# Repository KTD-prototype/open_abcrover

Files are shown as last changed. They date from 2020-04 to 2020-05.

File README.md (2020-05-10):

<!-- # open_abcrover -->

<div align="center">

</div>

<br>
<br>

- [Overview](#overview)
  - [General information](#general-information)
  - [How does it moves](#how-does-it-moves)
  - [Basic spesification](#basic-spesification)
- [Operability confirmed environments](#operability-confirmed-environments)
  - [PC environments (both develop and operate)](#pc-environments-both-develop-and-operate)
  - [Peripherals](#peripherals)
  - [Packages](#packages)
- [Parts list, assembly and wiring](#parts-list-assembly-and-wiring)
- [Install Software](#install-software)
  - [Install, download and build related packages](#install-download-and-build-related-packages)
  - [Prepare sub-onboard comtroller : arduino mega or equivalents](#prepare-sub-onboard-comtroller--arduino-mega-or-equivalents)
- [How to use](#how-to-use)
  - [Power source](#power-source)
  - [Check before operation](#check-before-operation)
  - [Launch!](#launch)
  - [Discription](#discription)

# Overview
## General information
This is an open source, affordable ground platform for remote-operated & autonomous driving experiments.
It is :  
* Simple and Expandable
    * Universal aluminum extruded beams, easy to mount your hardware. 
    * 3D printed brackets and mounts easy to be customized
    * Customizable software components built on ROS<sup>TM</sup> <sup>[1](#note1)</sup> and Arduino, easy to add your own software and electronics. 
  
* All terrain driving
    * High power motor and big wheel
    * Moderate size for indoor use, same foot print as domestic robotic vacuums
    * Convertible brackets to boost up wheel base and tread width for stable outdoor locomotion

* Affordable
  * Cheap and easy-to-by components
  * Minimum hardwares and electronics for remote operation can be built with around $400 USD or ¥40,000 JPY

<small id="note1">ROS is a trademark of Open Robotics.</small>

<br>

## How does it moves
Link to my youtube.  

(https://www.youtube.com/watch?v=tylhsJ_iiBY)

<br>

## Basic spesification
|General||
|:--|:--|
|Dimensions|W 250 * D 250 * H 250 [mm] at minimum assembly|
|Foot prints|350 [mm] diameter circle|
|Battery capacity|120 Wh for up to 2 hours operation|
|Ground clearance|55 [mm]|
|Total weight|4 [kg]|

|Chassis||
|:--|:--|
|Frames|20 * 20 [mm] aluminum beams|
|Brackets|3D printed with PETG or carbon PETG|
|Additionals|You can mount more beams and add your hardwares by M4 bolts and nuts.|

|Drive trains||
|:--|:--|
|Motors|Geared, brushed DC motor with 37mm diameter, 317rpm @maximum spped, 3.6N・m @stall by [servocity](https://www.servocity.com/317-rpm-spur-gear-motor-w-encoder)|
|Wheels|6 inch diameter, driven wheels|
|Casters|3 inch diameter, passive casters|

|Electronics||
|:--|:--|
|PC|[Jetson Nano Developer Kit (ver.B01)](https://developer.nvidia.com/embedded/jetson-nano-developer-kit)|
|MPU|[Arduino Mega 2560 REV3](https://store.arduino.cc/usa/mega-2560-r3)|
|IMU sensor|9 axis sensor [Adafruit BNO055](https://learn.adafruit.com/adafruit-bno055-absolute-orientation-sensor)|
|Motor encoders|mounted on each motor axes|
|Cameras|(*not used by default*)  Sainsmart IMX219 night vision camera module with 160° FOV, 8MP relosution, active IR flash (discontinued? [equivalents](https://www.sainsmart.com/products/sainsmart-imx219-night-vision-camera-module-for-nvidia-jetson-nano-board-8mp-sensor-77-degree-fov)) |

<br>
<br>

# Operability confirmed environments
The open ABC rover is developed and tested conditions below. Of course, you can make any changes and modifications along with your preferences.
## PC environments (both develop and operate)
* Ubuntu 18.04 LTS
  * python2.7.17
  * ROS melodic

## Peripherals
* Main on-board computer : [Jetson Nano Developer Kit(ver.B01)](https://developer.nvidia.com/embedded/jetson-nano-developer-kit)
* Sub on-board controller : [Arduino Mega 2560 REV3](https://store.arduino.cc/usa/mega-2560-r3)
* Joy stick : [Logitec F710 wireless gamepad](https://www.logitechg.com/en-us/products/gamepads/f710-wireless-gamepad.940-000117.html)

## Packages
* wheel odometry for differential-drive wheeled robot : [wheel_odometry](https://github.com/KTD-prototype/wheel_odometry)
* joy signal processing : [joy - ROS Wiki](http://wiki.ros.org/joy)
* velocity command generator from joy : [joy_teleop - ROS Wiki](http://wiki.ros.org/joy_teleop)

<br>
<br>

# Parts list, assembly and wiring
***Detailed documents are arriving soon!***

<br>

One noticeable feature of this rover is it's convertibility between outdoor mode and indoor mode.  

As you can see in a schematic iamge below, you can flip or offset the brackets so that you can boost up or shrink the rover's wheel base and tread width.  

At left side of the image, it's outdoor mode with bigger wheel base and tread width, to improve stability on rough terrain. At right side, it's indoor mode with less foot print to improve smooth movement in narrow area.  

<br>

left : outdoor mode, right : indoor mode
<div align="center">left : outdoor mode, right : indoor mode</div>

<br>
<br>

# Install Software
## Install, download and build related packages
Assume your workspace are named as ~/catkin_ws
```
$ cd ~/catkin_ws/src
$ git clone git@github.com:KTD-prototype/open_abcrover.git #main package
$ git clone git@github.com:KTD-prototype/wheel_odometry.git #wheel odometry package
$ sudo apt install ros-melodic-joy ros-melodic-joystick-teleop #additional packages
$ cd ~/catkin_ws
$ catkin_make
```

## Prepare sub-onboard comtroller : arduino mega or equivalents
Pick up codes from the directroy you've downloaded ; .../open_abcrover/scripts/arduino/open_abcrover_control_v1.0  

Upload them to your own board. The main file is named : open_abcrover_control_v1.0.ino

<br>
<br>

# How to use
## Power source
Any types of batteies can be used. In testing, I used two 4-cell Li-po batteries(14.8V at nominal voltage) One for motors, another for on-board computer with DCDC convirsion into 5V via BEC (battery eliminator circuitry)

In my choice, maximum voltage acceptable to motors are 12V. In those case, you have to regulate motor command by your own script.

Be careful to use Li-po or Li-ion batteries, not to over-charge, over-discharge, damage batteries!

<br>

## Check before operation
* Power source connection?
* All peripherals connected? (e.g. USB wireless receiver for your joystick)
* No shorted circuit? Be super-carefule especially around power source wiring such as terminal blocks.
* Wheels and boards are firmly mounted?

<br>

## Launch!
Type as bellow at your terminal.
```
$ roslaunch open_abcrover teleop_sample.launch
```

This file launchs all relative nodes to test default settings for remote operation via your joystick.

<br>

## Discription
**Remote operation**  
Once you launched as discripted above, you can drive the rover by your joy stick.
By default, you can enable remote operation by button LB, and get the rover move by left joystick. The maximum speed for this mode is around **1 km/h**.

Furthermore, you can enable **TURBO** mode to raise the maximum speed up to **4 km/h** , by pressing A button.

Button assignment and labels are according to joystick I used : [Locitech F710](https://www.logitechg.com/en-us/products/gamepads/f710-wireless-gamepad.940-000117.html) with **X-Input** mode.

<br>

**Nodes**
* **/joy_node** : Receive signals from joystick and send as commands from an operator
* **/teleop_twist_joy** : Receive commands from an operator and convert into velocity commands. Also regulates maximum gains of the velocity control by those paramters.
* **/velocity_controller** : Receive the velocity commands and convert into motor commands by PID control. Also receives joy command directly to check what operational mode the rover is.
* **/arduino_interface** : Receive the motor commands and send them to arduino. Receive IMU, encoder, battery voltage data and publish them.
* **/wheel_odometry** : Receive encoder data and calculate position, velocity and posture of the rover, and publish them.

<br>

**ROS Messages**  
* **/joy** : Raw commands from an operator
* **/teleop/cmd_vel** : Velocity command from an operator, with Twist message.
* **/motor_commands** : Motor comand for each two motors, calculated by PID controller in the velocity_controller node. Regulated not to exceed the motor capacity.
* **/operation_mode** : Indicates whether remote operation is enabled or not, turbo drive is enabled or not, and check joystick connection or other exceptional states of control system.
* **/encoder_2wheel** : Incremented encoder data from two motors.
* **/imu** : Imu data includes posture angle at quaternions, gyros, accelerometers.
* **/wheel_odometry** : Position, velocity and posture calculated by motor encoders.

Whole relationships of the nodes and messages are as bellow.



<br>

**Indicators**  
The code suppose to have two full-color LEDs on the rover's circuit, connnected to your arduino.
By default, each colors indicates as below:
* Blue : The rover is ready, but not engaged for remote operation.
* Green : Remote operation is engaged, maximum speed is 1 km/h approx.
* Yellow : Remote operation with turbo is engaged, maximum speed is 4 km/h approx.
* White : Autonomous driving is engaged (*planning to implement in future!*)
* Red : Communication link between on-board PC and joystick has lost. (*also for other exceptional states, in future!*)

The two LEDs will blinks when the battery voltages are getting low. By default, blinks every 0.75 seconds under 3.6 V/cell, every 0.25 seconds under 3.375 V/cell.

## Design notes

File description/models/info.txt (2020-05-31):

frame_indoor v8
コンポーネント インスタンス (1)
面積	0.761 m^2
密度	1781.903 kg / m^3
質量	2.842 kg
体積	0.002 m^3
物理マテリアル	(各種)

境界ボックス
	長さ 	 0.293 m
	幅 	 0.304 m
	高さ 	 0.179 m
ワールド座標系の X、Y、Z	0.00 m, 0.00 m, 0.00 m

原点の慣性モーメント   (kg m^2)
	Ixx = 0.019
	Ixy = -1.235E-04
	Ixz = -3.890E-05
	Iyx = -1.235E-04
	Iyy = 0.016
	Iyz = 7.486E-04
	Izx = -3.890E-05
	Izy = 7.486E-04
	Izz = 0.025
重心	5.102E-05 m, -0.003 m, -0.015 m

重心の慣性モーメント   (kg m^2)
	Ixx = 0.018
	Ixy = -1.240E-04
	Ixz = -4.109E-05
	Iyx = -1.240E-04
	Iyy = 0.016
	Iyz = 8.847E-04
	Izx = -4.109E-05
	Izy = 8.847E-04
	Izz = 0.025

frame_outdoor v4
コンポーネント インスタンス (1)
面積	0.761 m^2
密度	1756.987 kg / m^3
質量	2.802 kg
体積	0.002 m^3
物理マテリアル	(各種)

境界ボックス
	長さ 	 0.353 m
	幅 	 0.32 m
	高さ 	 0.179 m
ワールド座標系の X、Y、Z	0.00 m, 0.00 m, 0.00 m

原点の慣性モーメント   (kg m^2)
	Ixx = 0.022
	Ixy = -1.348E-04
	Ixz = 2.711E-05
	Iyx = -1.348E-04
	Iyy = 0.02
	Iyz = -2.730E-05
	Izx = 2.711E-05
	Izy = -2.730E-05
	Izz = 0.033
重心	-3.272E-04 m, -0.012 m, -0.017 m

重心の慣性モーメント   (kg m^2)
	Ixx = 0.021
	Ixy = -1.238E-04
	Ixz = 4.253E-05
	Iyx = -1.238E-04
	Iyy = 0.019
	Iyz = 5.335E-04
	Izx = 4.253E-05
	Izy = 5.335E-04
	Izz = 0.033

driven_wheel_left
コンポーネント インスタンス (1)
面積	0.118 m^2
密度	1140.149 kg / m^3
質量	0.216 kg
体積	1.895E-04 m^3
物理マテリアル	(各種)

境界ボックス
	長さ 	 0.045 m
	幅 	 0.152 m
	高さ 	 0.152 m
ワールド座標系の X、Y、Z	0.00 m, 0.00 m, 0.00 m

原点の慣性モーメント   (kg m^2)
	Ixx = 7.441E-04
	Ixy = -1.139E-08
	Ixz = 5.172E-08
	Iyx = -1.139E-08
	Iyy = 5.313E-04
	Iyz = 4.204E-08
	Izx = 5.172E-08
	Izy = 4.204E-08
	Izz = 5.311E-04
重心	0.025 m, 1.523E-05 m, -8.207E-05 m

重心の慣性モーメント   (kg m^2)
	Ixx = 7.441E-04
	Ixy = 7.205E-08
	Ixz = -3.981E-07
	Iyx = 7.205E-08
	Iyy = 3.923E-04
	Iyz = 4.177E-08
	Izx = -3.981E-07
	Izy = 4.177E-08
	Izz = 3.921E-04

driven_wheel_right
コンポーネント インスタンス (1)
面積	0.118 m^2
密度	1140.149 kg / m^3
質量	0.216 kg
体積	1.895E-04 m^3
物理マテリアル	(各種)

境界ボックス
	長さ 	 0.045 m
	幅 	 0.152 m
	高さ 	 0.152 m
ワールド座標系の X、Y、Z	0.00 m, 0.00 m, 0.00 m

原点の慣性モーメント   (kg m^2)
	Ixx = 7.441E-04
	Ixy = -1.139E-08
	Ixz = -5.172E-08
	Iyx = -1.139E-08
	Iyy = 5.313E-04
	Iyz = -4.204E-08
	Izx = -5.172E-08
	Izy = -4.204E-08
	Izz = 5.311E-04
重心	-0.025 m, -1.523E-05 m, -8.207E-05 m

重心の慣性モーメント   (kg m^2)
	Ixx = 7.441E-04
	Ixy = 7.205E-08
	Ixz = 3.981E-07
	Iyx = 7.205E-08
	Iyy = 3.923E-04
	Iyz = -4.177E-08
	Izx = 3.981E-07
	Izy = -4.177E-08
	Izz = 3.921E-04

caster_wheel
コンポーネント インスタンス (1)
面積	0.014 m^2
密度	930.00 kg / m^3
質量	0.082 kg
体積	8.836E-05 m^3
物理マテリアル	ゴム

境界ボックス
	長さ 	 0.02 m
	幅 	 0.075 m
	高さ 	 0.075 m
ワールド座標系の X、Y、Z	0.00 m, 0.00 m, 0.00 m

原点の慣性モーメント   (kg m^2)
	Ixx = 5.778E-05
	Ixy = 0.00
	Ixz = 0.00
	Iyx = 0.00
	Iyy = 3.163E-05
	Iyz = 0.00
	Izx = 0.00
	Izy = 0.00
	Izz = 3.163E-05
重心	0.00 m, 0.00 m, 0.00 m

重心の慣性モーメント   (kg m^2)
	Ixx = 5.778E-05
	Ixy = 0.00
	Ixz = 0.00
	Iyx = 0.00
	Iyy = 3.163E-05
	Iyz = 0.00
	Izx = 0.00
	Izy = 0.00
	Izz = 3.163E-05

caster_pivot
コンポーネント インスタンス (1)
面積	0.008 m^2
密度	7850.00 kg / m^3
質量	0.125 kg
体積	1.598E-05 m^3
物理マテリアル	鋼

境界ボックス
	長さ 	 0.03 m
	幅 	 0.04 m
	高さ 	 0.066 m
ワールド座標系の X、Y、Z	0.00 m, 0.00 m, 0.00 m

原点の慣性モーメント   (kg m^2)
	Ixx = 2.003E-04
	Ixy = 0.00
	Ixz = 0.00
	Iyx = 0.00
	Iyy = 2.033E-04
	Iyz = 3.322E-05
	Izx = 0.00
	Izy = 3.322E-05
	Izz = 3.133E-05
重心	0.00 m, 0.005 m, -0.034 m

重心の慣性モーメント   (kg m^2)
	Ixx = 5.411E-05
	Ixy = 0.00
	Ixz = 0.00
	Iyx = 0.00
	Iyy = 6.001E-05
	Iyz = 1.277E-05
	Izx = 0.00
	Izy = 1.277E-05
	Izz = 2.841E-05

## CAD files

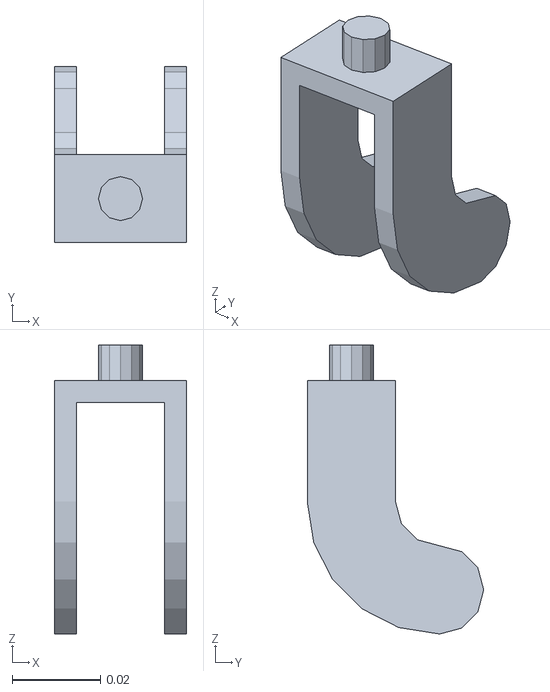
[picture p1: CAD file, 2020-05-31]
description/meshes/caster_pivot.stl
0.03 x 0.04 x 0.0655

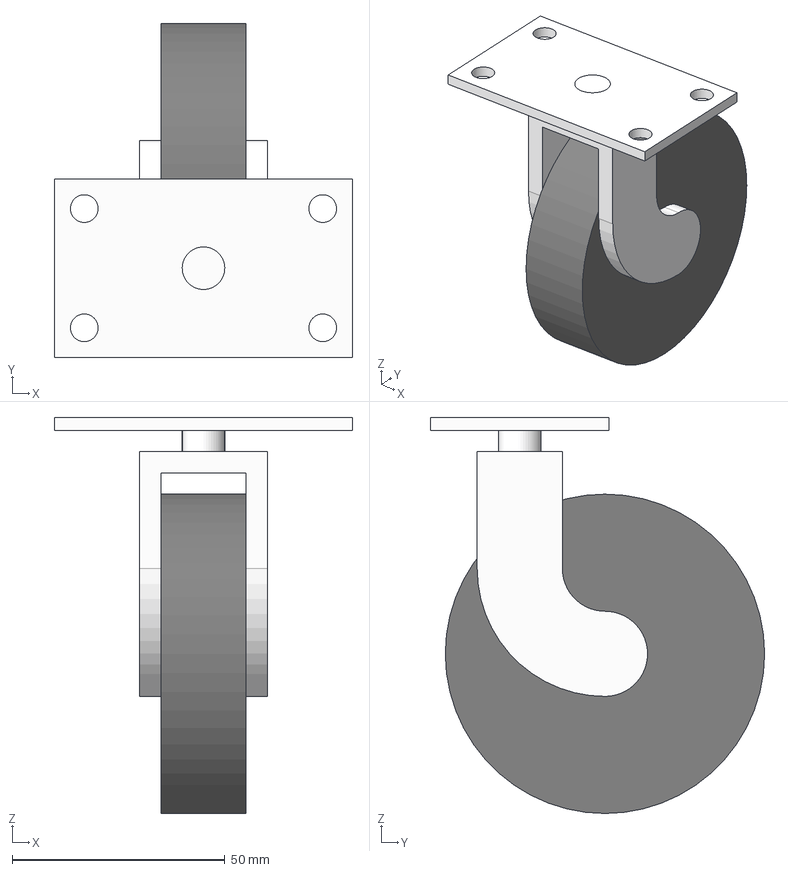
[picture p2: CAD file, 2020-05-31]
description/models/STEPfiles/caster.step
70.0 x 78.5 x 93.0 mm
wheel_base
wheel_stay_v2
caster_wheel_v2

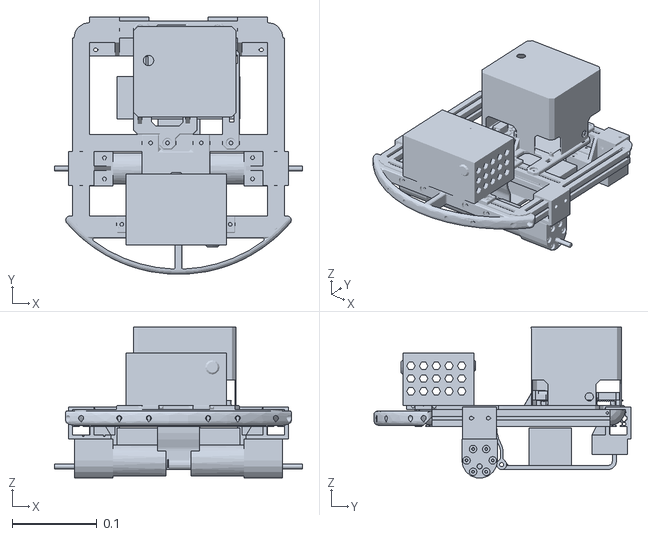
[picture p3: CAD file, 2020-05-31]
description/meshes/base_frame_indoor_v8.stl
0.293 x 0.304 x 0.178

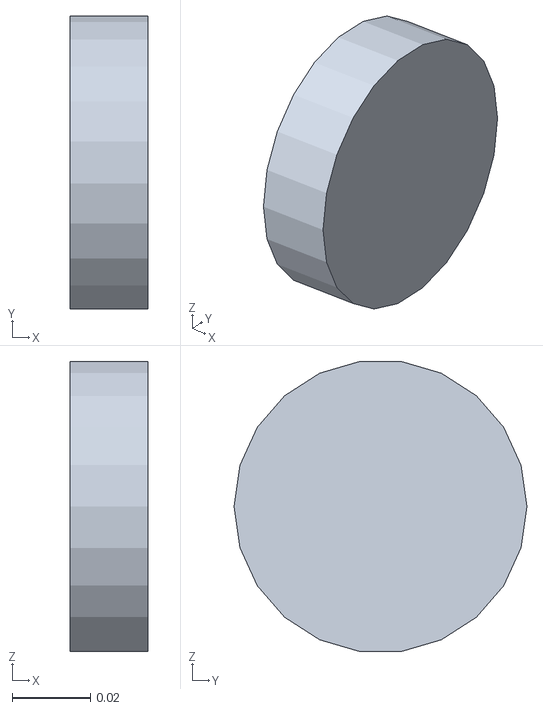
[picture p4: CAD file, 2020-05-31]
description/meshes/caster_wheel.stl
0.02 x 0.075 x 0.0742

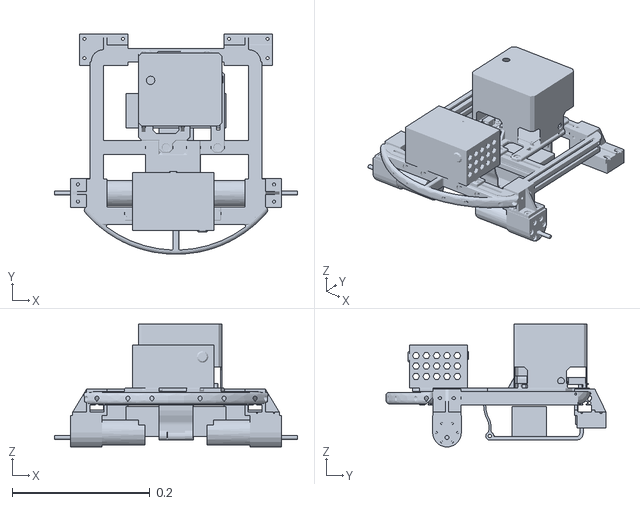
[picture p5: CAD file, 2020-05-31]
description/meshes/base_frame_outdoor_v4.stl
0.353 x 0.32 x 0.178

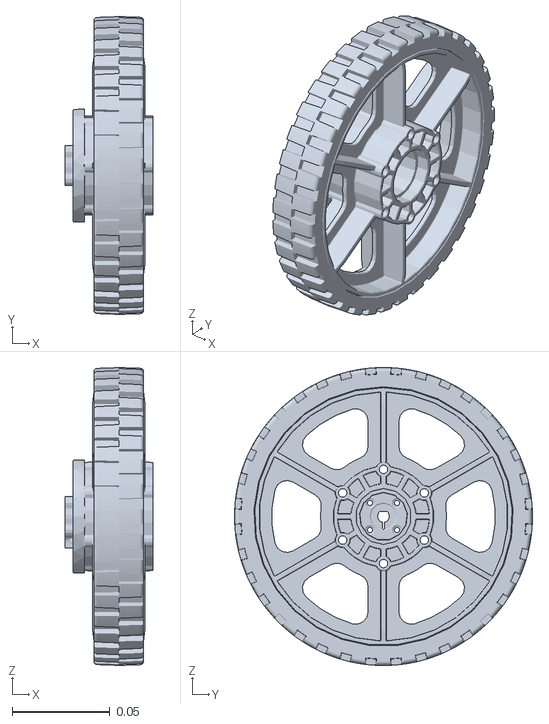
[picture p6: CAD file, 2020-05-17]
description/meshes/wheel_left.stl
0.0449 x 0.152 x 0.152

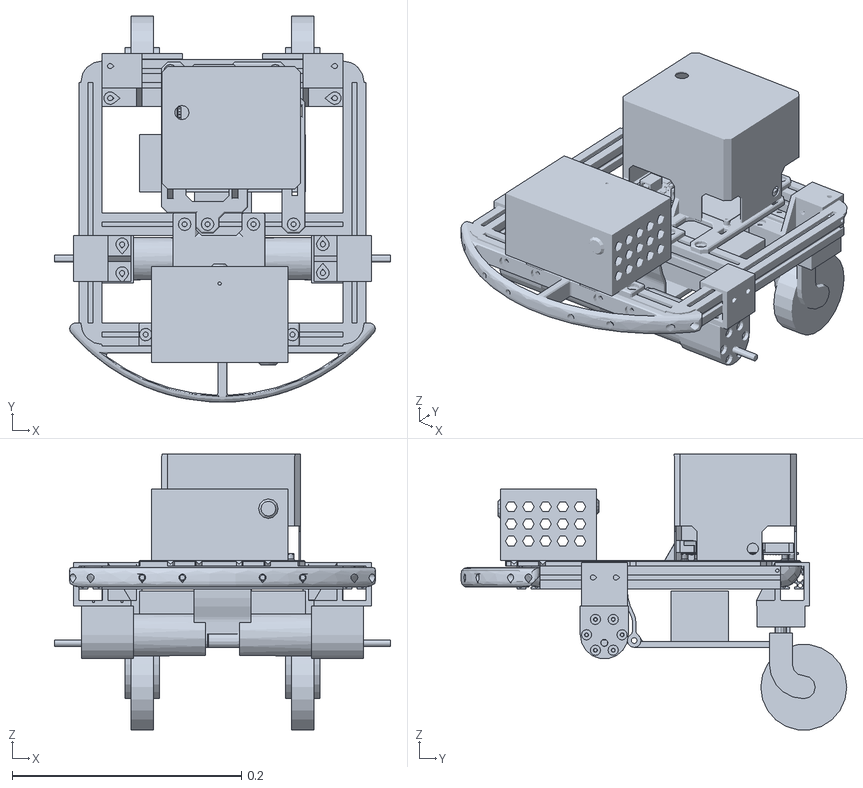
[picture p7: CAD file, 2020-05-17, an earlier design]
description/meshes/base_frame_indoor_v7.stl
0.293 x 0.336 x 0.24

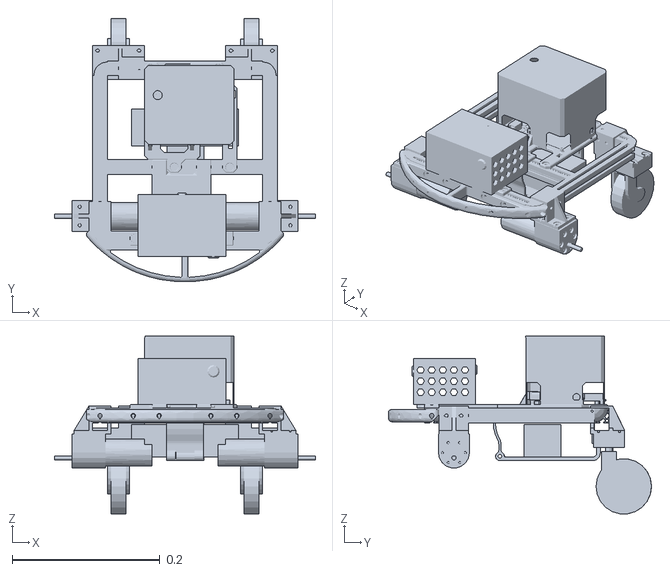
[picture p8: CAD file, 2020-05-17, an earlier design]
description/meshes/base_frame_outdoor_v3.stl
0.353 x 0.356 x 0.24

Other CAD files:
description/meshes/wheel_right.stl

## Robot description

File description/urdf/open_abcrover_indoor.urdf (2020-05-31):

<robot name="open_abcrover">
    <link name="base_footprint"/>

    <joint name="base_joint" type="fixed">
        <origin xyz="0 0 0.1332"/>
        <parent link="base_footprint"/>
        <child link="base_frame"/>
    </joint>

    <link name="base_frame">
        <visual>
            <geometry>
                <mesh filename="package://open_abcrover/description/meshes/base_frame_indoor_v8.stl"/>
            </geometry>
        </visual>
        <collision>
            <geometry>
                <mesh filename="package://open_abcrover/description/meshes/base_frame_indoor_v8.stl"/>
            </geometry>
        </collision>
        <inertial>
            <mass value="2.842"/>
            <inertia ixx="0.019" ixy="-1.235e-4" ixz="-3.89e-5" iyy="0.016" iyz="7.486e-4" izz="0.025"/>
        </inertial>
        <gazebo>
            <gravity>true</gravity>
        </gazebo>
    </link>

    <joint name="base_to_leftwheel" type="continuous">
        <origin xyz="0.1235 -0.0488 -0.057"/>
        <axis xyz="1 0 0"/>
        <parent link="base_frame"/>
        <child link="left_wheel"/>
    </joint>

    <link name="left_wheel">
        <visual>
            <geometry>
                <mesh filename="package://open_abcrover/description/meshes/wheel_left.stl"/>
            </geometry>
        </visual>
        <collision>
            <geometry>
                <mesh filename="package://open_abcrover/description/meshes/wheel_left.stl"/>
            </geometry>
        </collision>
        <inertial>
            <mass value="0.216"/>
            <inertia ixx="7.441e-4" ixy="-1.139e-8" ixz="5.172e-8" iyy="5.313e-4" iyz="4.204e-8" izz="5.311e-04"/>
        </inertial>
    </link>

    <joint name="base_to_rightwheel" type="continuous">
        <origin xyz="-0.1235 -0.0488 -0.057"/>
        <axis xyz="1 0 0"/>
        <parent link="base_frame"/>
        <child link="right_wheel"/>
    </joint>

    <link name="right_wheel">
        <visual>
            <geometry>
                <mesh filename="package://open_abcrover/description/meshes/wheel_right.stl"/>
            </geometry>
        </visual>
        <collision>
            <geometry>
                <mesh filename="package://open_abcrover/description/meshes/wheel_right.stl"/>
            </geometry>
        </collision>
        <inertial>
            <mass value="0.216"/>
            <inertia ixx="7.441e-4" ixy="-1.139e-8" ixz="-5.172e-8" iyy="5.313e-4" iyz="-4.204e-8" izz="5.311e-04"/>
        </inertial>
    </link>


    <joint name="base_to_leftcaster_pivot" type="continuous">
        <origin xyz="0.07 0.10515 -0.0402"/>
        <axis xyz="0 0 1"/>
        <parent link="base_frame"/>
        <child link="left_caster_pivot"/>
    </joint>

    <link name="left_caster_pivot">
        <visual>
            <geometry>
                <mesh filename="package://open_abcrover/description/meshes/caster_pivot.stl"/>
            </geometry>
        </visual>
        <collision>
            <geometry>
                <mesh filename="package://open_abcrover/description/meshes/caster_pivot.stl"/>
            </geometry>
        </collision>
        <inertial>
            <mass value="0.125"/>
            <inertia ixx="2.003e-4" ixy="0" ixz="0" iyy="2.033e-4" iyz="3.322e-5" izz="3.133e-05"/>
        </inertial>
    </link>

    <joint name="left_caster_pivot_to_wheel" type="continuous">
        <origin xyz="0 0.02 -0.0555"/>
        <axis xyz="1 0 0"/>
        <parent link="left_caster_pivot"/>
        <child link="left_caster_wheel"/>
    </joint>

    <link name="left_caster_wheel">
        <visual>
            <geometry>
                <mesh filename="package://open_abcrover/description/meshes/caster_wheel.stl"/>
            </geometry>
        </visual>
        <collision>
            <geometry>
                <mesh filename="package://open_abcrover/description/meshes/caster_wheel.stl"/>
            </geometry>
        </collision>
        <inertial>
            <mass value="0.082"/>
            <inertia ixx="5.778e-5" ixy="0" ixz="0" iyy="3.163e-5" iyz="0" izz="3.163e-05"/>
        </inertial>
    </link>

    <joint name="base_to_rightcaster_pivot" type="continuous">
        <origin xyz="-0.07 0.10515 -0.0402"/>
        <axis xyz="0 0 1"/>
        <parent link="base_frame"/>
        <child link="right_caster_pivot"/>
    </joint>

    <link name="right_caster_pivot">
        <visual>
            <geometry>
                <mesh filename="package://open_abcrover/description/meshes/caster_pivot.stl"/>
            </geometry>
        </visual>
        <collision>
            <geometry>
                <mesh filename="package://open_abcrover/description/meshes/caster_pivot.stl"/>
            </geometry>
        </collision>
        <inertial>
            <mass value="0.125"/>
            <inertia ixx="2.003e-4" ixy="0" ixz="0" iyy="2.033e-4" iyz="3.322e-5" izz="3.133e-05"/>
        </inertial>
    </link>

    <joint name="right_caster_pivot_to_wheel" type="continuous">
        <origin xyz="0 0.02 -0.0555"/>
        <axis xyz="1 0 0"/>
        <parent link="right_caster_pivot"/>
        <child link="right_caster_wheel"/>
    </joint>

    <link name="right_caster_wheel">
        <visual>
            <geometry>
                <mesh filename="package://open_abcrover/description/meshes/caster_wheel.stl"/>
            </geometry>
        </visual>
        <collision>
            <geometry>
                <mesh filename="package://open_abcrover/description/meshes/caster_wheel.stl"/>
            </geometry>
        </collision>
        <inertial>
            <mass value="0.082"/>
            <inertia ixx="5.778e-5" ixy="0" ixz="0" iyy="3.163e-5" iyz="0" izz="3.163e-05"/>
        </inertial>
    </link>


    <gazebo>
        <plugin name="differential_drive_controller" filename="libgazebo_ros_diff_drive.so">
            <leftJoint>base_to_leftwheel</leftJoint>
            <rightJoint>base_to_rightwheel</rightJoint>
            <robotBaseFrame>base_footprint</robotBaseFrame>
            <wheelSeparation>0.298</wheelSeparation>
            <wheelDiameter>0.1524</wheelDiameter>
            <publishWheelJointState>true</publishWheelJointState>
        </plugin>

        <plugin name="joint_state_publisher" filename="libgazebo_ros_joint_state_publisher.so">
            <jointName>base_to_leftwheel, base_to_rightwheel</jointName>
        </plugin>
    </gazebo>

    <gazebo>
        <plugin name="joint_state_publisher" filename="libgazebo_ros_joint_state_publisher.so">
            <jointName>base_to_leftcaster_pivot, left_caster_pivot_to_wheel, base_to_rightcaster_pivot, right_caster_pivot_to_wheel</jointName>
        </plugin>
    </gazebo>
</robot>

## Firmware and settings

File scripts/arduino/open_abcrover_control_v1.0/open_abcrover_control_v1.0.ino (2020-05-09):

/* Following is License message for Adafruit library : https://github.com/adafruit/Adafruit_BNO055.
-----------------start of the message---------------------
MIT License

Copyright (c) 2018 Adafruit Industries

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
THE SOFTWARE IS PROVIDED "AS IS", WITHOUT WARRANTY OF ANY KIND, EXPRESS OR
IMPLIED, INCLUDING BUT NOT LIMITED TO THE WARRANTIES OF MERCHANTABILITY,
FITNESS FOR A PARTICULAR PURPOSE AND NONINFRINGEMENT. IN NO EVENT SHALL THE
AUTHORS OR COPYRIGHT HOLDERS BE LIABLE FOR ANY CLAIM, DAMAGES OR OTHER
LIABILITY, WHETHER IN AN ACTION OF CONTRACT, TORT OR OTHERWISE, ARISING FROM,
OUT OF OR IN CONNECTION WITH THE SOFTWARE OR THE USE OR OTHER DEALINGS IN THE
SOFTWARE.
-----------------end of the message---------------------
and this is build on adafruit unified sensor driver : https://github.com/adafruit/Adafruit_Sensor */


/* Following is License message for DualVNH5019MotorShield : https://github.com/pololu/dual-vnh5019-motor-shield
-----------------start of the message---------------------
Copyright (c) 2014 Pololu Corporation.  For more information, see

http://www.pololu.com/
http://forum.pololu.com/

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
THE SOFTWARE IS PROVIDED "AS IS", WITHOUT WARRANTY OF ANY KIND,
EXPRESS OR IMPLIED, INCLUDING BUT NOT LIMITED TO THE WARRANTIES
OF MERCHANTABILITY, FITNESS FOR A PARTICULAR PURPOSE AND
NONINFRINGEMENT. IN NO EVENT SHALL THE AUTHORS OR COPYRIGHT
HOLDERS BE LIABLE FOR ANY CLAIM, DAMAGES OR OTHER LIABILITY,
WHETHER IN AN ACTION OF CONTRACT, TORT OR OTHERWISE, ARISING
FROM, OUT OF OR IN CONNECTION WITH THE SOFTWARE OR THE USE OR
OTHER DEALINGS IN THE SOFTWARE.
-----------------end of the message--------------------- */


#include <TimerOne.h>
#include <Wire.h>
#include <Adafruit_Sensor.h>
#include <Adafruit_BNO055.h>
#include <utility/imumaths.h>
#include "DualVNH5019MotorShield.h"
#include <Adafruit_NeoPixel.h>

// constants for an IMU
#define GRAVITATIONAL_ACCEL 9.798 //at TOKYO
#define IMU_SAMPLERATE_HZ 100     //refresh rate of the imu (looks like it should be fixed at 100Hz due to bno055 hardware...?)

// constants for pin assign
#define ENC_LA 2            // input from encoder, left motor, phaseA
#define ENC_LB 3            // left motor phaseB
#define ENC_RA 18           // right motor, phaseA
#define ENC_RB 19           // right motor, phaseB
#define VOLTAGE_MONITOR1 A2 // voltage monitor
#define VOLTAGE_MONITOR2 A3 // voltage monitor
#define LED_BUILTIN 13      // CAUTION! used by the motor drivers
#define ALERT_LED 52        // a pin the series of full-color LEDs are connected
#define NUMPIXELS 2         // the number of full-color LEDs

// constants for motors
#define PULSE_PER_ROUND 723.24 // encoder pulse resolution * gear ratio
#define MAXIMUM_OUTPUT 300     // maximum pwm output for motor

// flag to control whether timer interruption is ignited or not
volatile bool timer_interrupt_flag = false;
volatile bool imu_refresh_enable = true;

//paramters to count time
int time1, time2, time3, past_time;

//parameters for motors/encoders
volatile byte pulse_L, last_pulse_L, pulse_R, last_pulse_R;
volatile long encoder_count_L = 0, encoder_count_R = 0;

// prepare parameters for motor output before receiving commands
int operation_mode = 0; // 0:disabiled, 1:teleop, 2:teleop_turbo, 3:autonomous
int command_L = 0, command_R = 0;

//parameters to store IMU data
float quaternions[4] = {0.0, 0.0, 0.0, 0.0}; //x,y,z,w
float accelerometers[3] = {0.0, 0.0, 0.0};   //x,y,z
float gyros[3] = {0.0, 0.0, 0.0};            //roll,pitch,yaw

// Check I2C device address and correct line below (by default address is 0x29 or 0x28)
//                                   id, address
Adafruit_BNO055 bno = Adafruit_BNO055(-1, 0x28);

// pin remap of the motor sheild
//                       1a,1b,1pw,1e,1cs,2a,2b,2pw,2e,2cs
DualVNH5019MotorShield md(13, 4, 9, 6, A0, 7, 8, 10, 12, A1);

// initialize full color LED
Adafruit_NeoPixel pixels(NUMPIXELS, ALERT_LED, NEO_GRB + NEO_KHZ800);

void setup()
{
        // timer interrupt initialization
        Timer1.initialize(1000000 / IMU_SAMPLERATE_HZ);
        Timer1.attachInterrupt(interrupt);

        // serial communication initialization
        Serial.begin(230400);

        /* Initialise the bno055_imu */
        if (!bno.begin())
        { /* There was a problem detecting the BNO055 ... check your connections */
                Serial.print("Ooops, no BNO055 detected ... Check your wiring or I2C ADDR!");
                while (1)
                        ;
        }
        delay(100);
        bno.setExtCrystalUse(true);

        // initialize the motor driver shield
        md.init();

        // change bitrate of I2C comm to 400kbps (100kbps, usual)
        Wire.setClock(400000);

        // change pwm frequency
        TCCR2B = (TCCR2B & 0b11111000) | 0x01; //31.37255 [kHz]
        // TCCR2B = (TCCR2B & 0b11111000) | 0x02; //3.92116 [kHz]
        // TCCR2B = (TCCR2B & 0b11111000) | 0x03; //980.39 [Hz]
        // TCCR2B = (TCCR2B & 0b11111000) | 0x04; //490.20 [Hz]
        // TCCR2B = (TCCR2B & 0b11111000) | 0x05; //245.10 [Hz]
        // TCCR2B = (TCCR2B & 0b11111000) | 0x06; //122.55 [Hz]
        // TCCR2B = (TCCR2B & 0b11111000) | 0x07; //30.64 [Hz]

        pixels.begin(); // INITIALIZE NeoPixel strip object (REQUIRED)

        // setup arduino GPIO
        pinMode(ENC_LA, INPUT_PULLUP);
        pinMode(ENC_LB, INPUT_PULLUP);
        pinMode(ENC_RA, INPUT_PULLUP);
        pinMode(ENC_RB, INPUT_PULLUP);

        // pinMode(LED_BUILTIN, OUTPUT);

        // setup hardware interrupt
        attachInterrupt(0, encoder_read, CHANGE); // pin2 to left encoder phase A
        attachInterrupt(1, encoder_read, CHANGE); // pin3 to left encoder phase B
        attachInterrupt(5, encoder_read, CHANGE); // pin18 to right encoder phase A
        attachInterrupt(4, encoder_read, CHANGE); // pin19 to right encoder phase B
}

void loop()
{
        if (timer_interrupt_flag == true)
        { // get imu data at timer interruption
                get_quaternion_data(quaternions);
                get_accelerometer_data(accelerometers);
                get_gyro_data(gyros);
                timer_interrupt_flag = false; // toggle the flag again
        }

        // check the battery voltage (divided by 4, from 14.8V to 3.7V at nominal voltage)
        float battery_voltage[2] = {0.0, 0.0};
        battery_voltage[0] = -0.664 + float(analogRead(VOLTAGE_MONITOR1)) * 4.0 * 5.0 / 1023.0;
        battery_voltage[1] = -0.664 + float(analogRead(VOLTAGE_MONITOR2)) * 4.0 * 5.0 / 1023.0;
        // offset is needed(currently, -0.664[V]) is needed and the offset value depends on your host PC (?)

        // communicate with host PC
        if (Serial.available() > 1)
        { //6 bytes should be received, but arduino hangs up when you wait all 6 bytes are available
                if (Serial.read() == 'H')
                { //only when received data starts from 'H'
                        delayMicroseconds(200);
                        // read data : operation mode
                        operation_mode = Serial.read();

                        // read data : pwm command for motors and shift it
                        int offset = 300; // the value depends how much did you offset befor sending the commands
                        command_L = receive_data() - offset;
                        command_R = receive_data() - offset;

                        // drive motors
                        if (operation_mode == 4)
                        { // if there is something wrong
                                // motor_drive(0, 0);
                                command_L = 0;
                                command_R = 0;
                        }
                        else if (battery_voltage[1] < 13.5)
                        { //if the battery is running out
                                // motor_drive(0, 0);
                                command_L = 0;
                                command_R = 0;
                        }
                        motor_drive(command_L, command_R);

                        // send data : data of encoders and IMU
                        Serial.println(encoder_count_L);
                        Serial.println(encoder_count_R);
                        Serial.println(quaternions[0]);
                        Serial.println(quaternions[1]);
                        Serial.println(quaternions[2]);
                        Serial.println(quaternions[3]);
                        Serial.println(accelerometers[0]);
                        Serial.println(accelerometers[1]);
                        Serial.println(accelerometers[2]);
                        Serial.println(gyros[0]);
                        Serial.println(gyros[1]);
                        Serial.println(gyros[2]);
                        // Serial.println(Serial.available());

                        // if com speed is fast enough
                        Serial.println(battery_voltage[0]);
                        Serial.println(battery_voltage[1]);

                        // to check the commands sent to motor driver
                        // Serial.println(command_L);
                        // Serial.println(command_R);

                        //flush buffer and wait to complete sending
                        // Serial.flush();
                        // while(Serial.available()) {
                        //         Serial.read();
                        // }
                }
        }

        // rover state indicator
        rover_state_indicator(operation_mode, battery_voltage);
}

// function for timer interrupt : toggle the flag and process will be in the main.
void interrupt()
{
        timer_interrupt_flag = true;
}

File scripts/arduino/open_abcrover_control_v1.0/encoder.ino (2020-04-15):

// func at the HW interrupt. read encoders.
void encoder_read() {
        //  refresh each value if it is changed
        //  handle those as a single 2 bit number; 1st bit is High/Low of A, 2nd bit is High/Low of B
        //  e.g.1: if pulse A is HIGH, pulse value is 1. Shift it to left, then you get 10. if pulse B is also high, add it to the 10, then you get 11, as a combined information of the A and B
        //  e.g.2: if pulse A is LOW, pulse value is 0. Shift it to left, then you get 00. if pulse B is hig
        pulse_L = !digitalRead(ENC_LA) << 1;
        pulse_L += !digitalRead(ENC_LB);
        pulse_R = !digitalRead(ENC_RA) << 1;
        pulse_R += !digitalRead(ENC_RB);

        //  pulse_L will incremented as 0, 01(1), 11(3), 10(2) or reversed order of them.
        //  exchange value of 2 & 3 since this order is a bit confusing.
        pulse_L = process_byte(pulse_L);
        pulse_R = process_byte(pulse_R);

        // count up encoder(way to increment the count should be different between left and right)
        encoder_count_L = count_encoder(pulse_L, last_pulse_L, encoder_count_L, 'L');
        encoder_count_R = count_encoder(pulse_R, last_pulse_R, encoder_count_R, 'R');

        //  reserve pulse info as last one of those
        last_pulse_L = pulse_L;
        last_pulse_R = pulse_R;
}


byte process_byte(byte pulse) {
        if (pulse == 3) {
                pulse = 2;
        }
        else if (pulse == 2) {
                pulse = 3;
        }
        return pulse;
}



long count_encoder(byte pulse, byte last_pulse, long count, char L_or_R) {
        // process for left motor encoder
        if (L_or_R == 'L') {
                //  exception process
                if (pulse == last_pulse) {
                        //  do nothing when encoder signal has chattered.
                }
                else if (pulse == 0 && last_pulse == 3) {
                        count--;
                }
                else if (pulse == 3 && last_pulse == 0) {
                        count++;
                }

                //  counting encoder;main process
                else if (abs(pulse - last_pulse) > 1) {
                        // do nothing when encoder signal has hopped(= chattering).
                }

                else if (pulse > last_pulse) {
                        count--;
                }
                else {
                        count++;
                }
        }


        // process for right motor encoder
        else if (L_or_R == 'R') {
                //  exception process
                if (pulse == last_pulse) {
                        //  do nothing when encoder signal has chattered.
                }
                else if (pulse == 0 && last_pulse == 3) {
                        count++;
                }
                else if (pulse == 3 && last_pulse == 0) {
                        count--;
                }

                //  counting encoder;main process
                else if (abs(pulse - last_pulse) > 1) {
                        // do nothing when encoder signal has hopped(= chattering).
                }

                else if (pulse > last_pulse) {
                        count++;
                }
                else {
                        count--;
                }
        }
        return count;
}

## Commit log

2020-03-28 add functions to count up encoder
2020-03-28 add motor drive function
2020-03-29 cleaned the code and add battery monitor function
2020-04-01 add arduino interface node
2020-04-06 add function to shift pwm data
2020-04-07 add velocity controler functions
2020-04-12 test velocity control
2020-04-13 modified to increase resolution of motor drive command
2020-04-13 modified to increase resolution of motor drive command and changed parameter name
2020-04-13 tested velocity control
2020-04-14 modified velocity control functions
2020-04-14 tuned gains of velocity control
2020-04-16 tuned gains for velocity control
2020-04-19 add gyro and accelerometers data to publish
2020-04-19 add rovor state indicator based on blink pattern of LEDs
2020-04-20 made python class for arduino interface and reorganized the files
2020-04-22 add safety function in case communication with joystick is lost
2020-04-29 change offset value of battery voltage measurement
2020-05-06 purge I control from velocity control
2020-05-10 remap ros message for velocity command : /cmd_vel for teleop
2020-05-17 add description file
    [base_frame_indoor.stl, base_frame_outdoor.stl, open_abcrover_indoor.urdf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]
2020-05-17 add files for urdf display
2020-05-17 add description files
    [open_abcrover_outdoor.urdf]
2020-05-19 add inertia info
    [open_abcrover_indoor.urdf]
2020-05-31 update robot models:add free casters
    [base_frame_indoor.stl, base_frame_indoor_v7.stl, base_frame_indoor_v8.stl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]
2020-05-31 updated files for gazebo
    [open_abcrover_indoor.urdf]
2020-05-31 add files for realsense simulation
    [_d435.gazebo.xacro, _d435.urdf.xacro, indoor_realsense_test.urdf]
